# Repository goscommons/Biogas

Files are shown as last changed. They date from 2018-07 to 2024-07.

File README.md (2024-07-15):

# Mesophilic Biodigester
## validated design
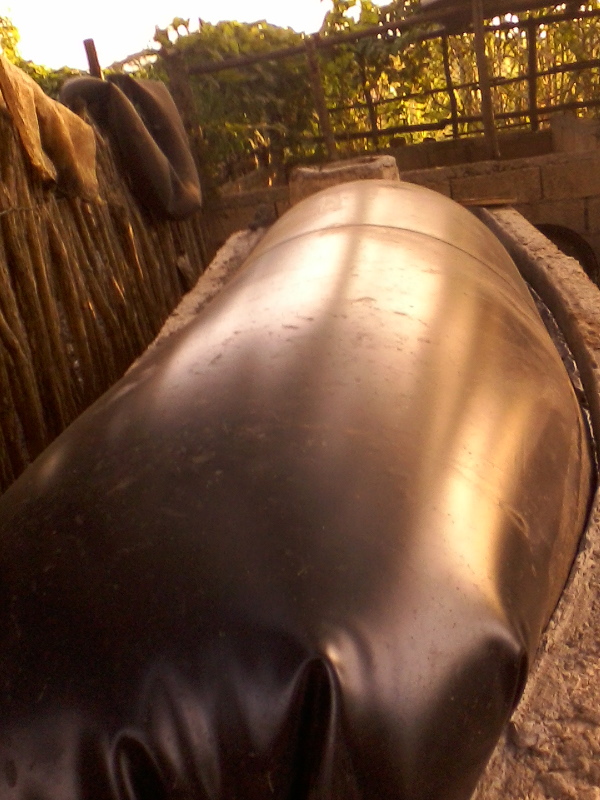
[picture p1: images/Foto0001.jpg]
Name of the machine


For more foto's (and some text) see [Fabrication.md](Fabrication.md).

## Purpose of this digester
Small biodigesters like the one on the foto, made in juli 2018, can be used in the context of family farms to improve life quality in an ecological way. Apart from considerable ecological impact by generating a truly closed loop of resources it also has economical benefits in several ways.
From the various types of installations that exist we chose the Plug-Flow type, the one on the foto cost about 125 dollar in Cuba. Waste generated by humans and/or animals can be processed by this device to produce biogas and fertilizers. This particular type of digester is espcially suitable for tropical and high temperature areas because it works best with a tank liquid temperature of 37 C (99 F).
## How it works
> A biodigester is like a mechanical stomach. It is fed with organic material, which is broken down (decomposed) by micro-organisms (bacteria) in an oxygen-free (anaerobic) environment to produce renewable energy in the form of biogas as well as an exceptionally good fertilizer.
> Anaerobic digestion is a collection of processes by which micro organisms break down biodegradable material in the absence of oxygen.[1] The process is used for industrial or domestic purposes to manage waste and to produce fuel.

## Use context
This biodigester can be used to process pig, cow and other kind of biomatter and probably agricutural waste like banana trees can be digested too.
The biodigester generates economic and ecologic value.
In the first place it produces biogas which can be used for cooking. For this reason these installations are often referred to as biogas plants.
Secondly it produces an excelent natural organic fertilizer that is used for the crops of the farm. This organic fertilizer has the following advantages:
1. It protects and enriches the soil structure in contrast with industrial fertilizers and pesticides.
2. The farmer does not need to buy potasium or other chemical fertilizers.
3. The farmer does not need pesticides anymore or very little because the fertilizer makes the crops healthier and therefore more resistent against deseases and parasites.
4. The crop yield could be higher because the crops are healthier. We will do some testing to see the effect on banana trees.

## Design specifications
- The tank has a size of 300x100x100 cm exterior and 270x70x100 cm interior. The designed liquid hight is about 90 cm giving the installation a total of 1.8 m3 capacity.
- For the outlet any pipe or rigid tube with an inner diameter of 2cm or more can be used.
- The inlet pipe should have an inner diameter of at least 10cm.
- The gas outlet could be placed anywhere on the foil preferably using plastic components and a tube of at least 0.8 cm diameter.
- To attach the foil in a way that no gas can escape we chose to attach it to the tank wall some 40 cm from the top of the wall. Of course when no gas is used the liquid would be pressed down, eventually forcing the gas out of the tank to the air. The gas usage must keep up to the speed at which it is produced.

## References
1. [Retrieved "Remember the biodigester"](https://www.src.sk.ca/blog/remember-biodigester)
1. [Find more in wkikipedia](https://en.wikipedia.org/wiki/Anaerobic_digestion)

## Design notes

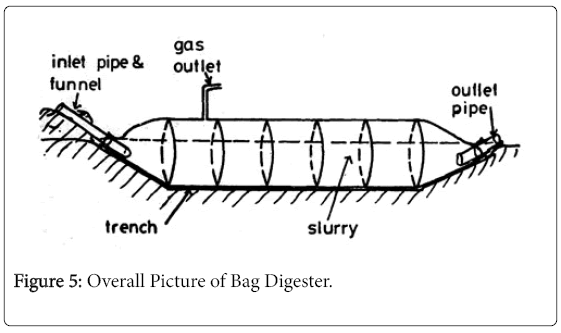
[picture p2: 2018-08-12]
images/functional diagram.png

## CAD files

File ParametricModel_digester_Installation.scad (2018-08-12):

/*A rectangular brick pool that is normally used when bulding small farm biodigesters.*/

// Make an estimate of the size of the digester pool
el=200;//estimated length
ew=100;//estimated width
eh=50;//estimated height

//Adjust brick dimensions
l=21.5;//brick length
w=10.5;//brick width
h=10.5;//brick height

// This section normalizes the dimension between estimate and real brick dimensions
dl=round(el/l)*l;//real length
dw=round(ew/l)*l;// real width
dh=round(eh/h)*h;// real height

// Create wall with proper positioning of bricks
module l_wall(inv,dist,lg,zlg){
    module l_line(dist,lg){
    for (i=[0:lg-1])
      if(i*dist<=dl){
        if(i%2==0){
            translate([0,i*(dist),0])
                cube(size=[w,l,h], center=false);
        }
        else{
            translate([0,i*(dist),0])
            color("red")
            cube(size=[w,l,h], center=false);
        
        }
    }
    else{
        }

}
    if (inv==true)
    for (z=[0:zlg]){
            if(z%2==0){
                translate([0,l/2,z*h])
                l_line(dist,lg);
                }
            else{
                translate([0,0,z*h])
                l_line(dist,lg);
                }
            }    
    else
    for (z=[0:zlg]){
            if(z%2!=0){
                translate([0,l/2,z*h])
                l_line(dist,lg);
                }
            else{
                translate([0,0,z*h])
                l_line(dist,lg);
                } 
        
    }

}


translate([0,0,0])l_wall(false,l,dl/l,dh/h);
translate([dw,0,0])l_wall(true,l,dl/l,dh/h);
translate([0,dl+w,0])rotate([0,0,-90])l_wall(false,l,dw/l,dh/h);
translate([0,w,0])rotate([0,0,-90])l_wall(true,l,dw/l,dh/h);

echo("you need in total: ",round(el/l*2)*round(eh/h)+ round(ew/l*2)*round(eh/h)," bricks to build this pool");

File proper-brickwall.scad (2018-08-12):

/*This is just a very basic model that generates the brick reservoir based on the size of the digester*/

/*Digester Size*/
dl=200;//length
dw=100;//width
dh=50;


/*Brick Parameters*/
h=10.5;//height
w=10.5;//width
l=21.5;//length

i_end=dl/l;
z_end=dw/l;
y_end=dh/h;



//brick line
module l_line(dist){
for (i=[0:i_end])
translate([0,i*(dist+dist*0.05),0])
 cube(size=[w,l,h], center=true);
}

module w_line(dist){
for (i=[0:z_end])
rotate(-90,30,0)
translate([0,i*(dist+dist*0.05),0])
 cube(size=[w,l,h], center=true);
}



// Create wall with proper positioning of bricks
module l_wall(){
    for (i=[0:y_end])
        if (i%2==0){
        translate([0,l/2,i*(h+(h*0.05))])
        l_line(l);
        }
    else{
        translate([0,0,i*(h+(h*0.05))])
        l_line(l);
        }
}

//w_line(l);




l_wall();
//mirror([0,1,0])l_wall();

rotate([0,0,180])
color("lime")
translate([-dw,-dl,0])
l_wall();

//translate([0,0,0])color("red")w_wall();

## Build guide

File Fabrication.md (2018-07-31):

# Biogas
Biogas for small farm

Here are the first photos of the installation. Not much details to be seen here yet, but we are just starting to describe the installation.

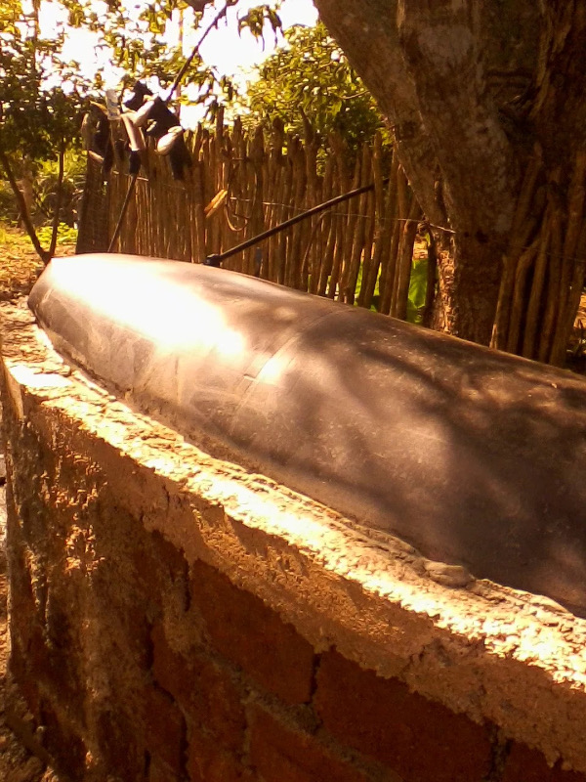
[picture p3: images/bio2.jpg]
Bio gas tank


We used pond foil to cover the tank and hold the gases as produced by the microbes. Since the cover must be air tight, we decided that it would be best to attache it to the tank well below liquid level.

From this photo you can see pieces of electricity (gauge 10) wire coming out of the wall some 40 cm from the top of the tank. These were used to attach the cover. You can also see where the inlet is going to be located.

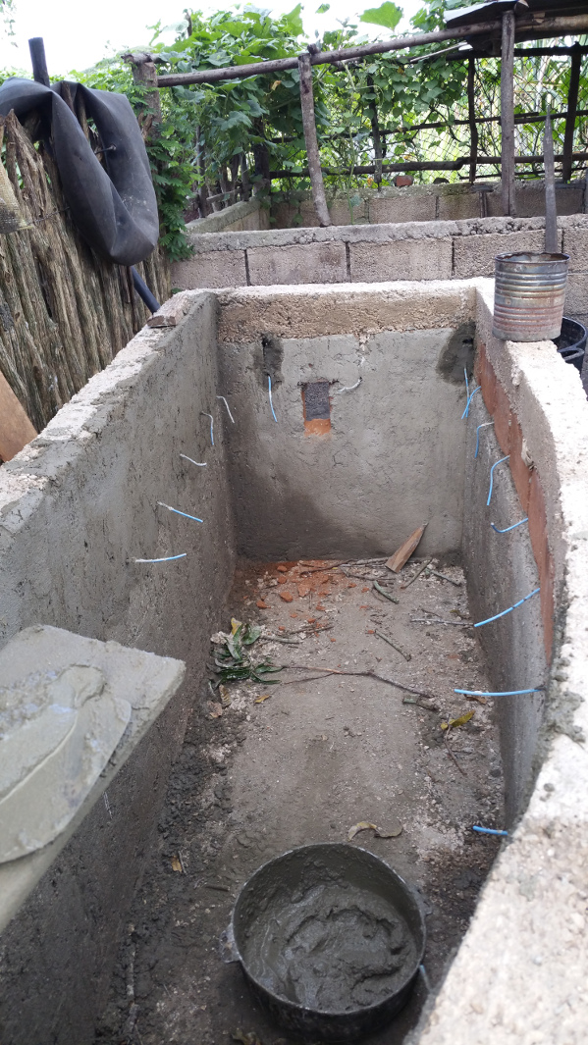
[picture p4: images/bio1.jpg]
Construction of the tank


Here you see a view from the outlet side of the tank. At the far end you can see the inlet mounted on top of the tank border.

Outlet side of the tank

Here you can see the beautiful blue flame of the gas. An installation like this produces about 50 percent methane (MH4) and 50 percent carbon dioxide (CO2), and some, but generally very little hydrogene sulfide (H2S). We have not yet done any filtering. We will add a filter to get rid of the H2S if it turns out to produce a noticeble smell (of rotten eggs).

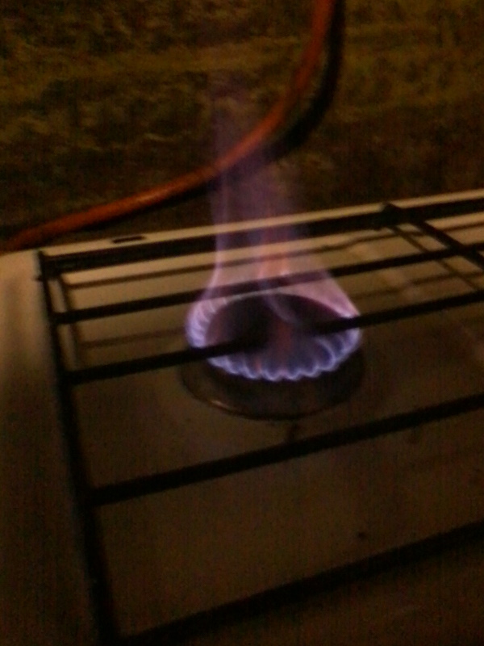
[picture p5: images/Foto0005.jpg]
Flame of the gas stove


Here is another photo of the stove with a pot over the flame.

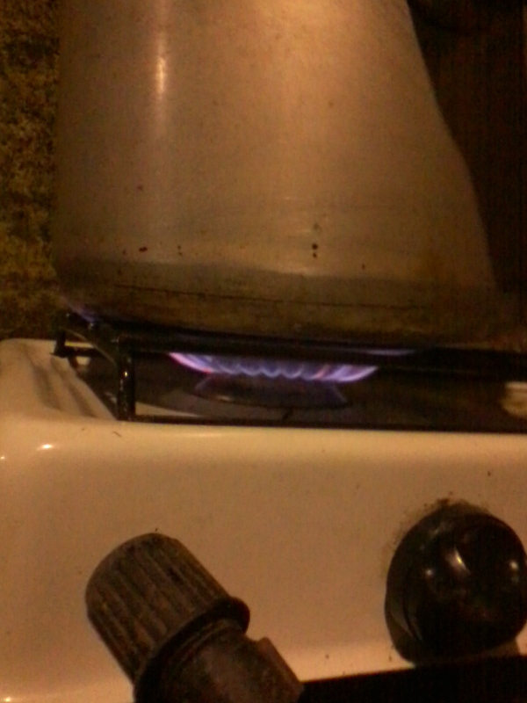
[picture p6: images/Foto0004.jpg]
Flame with pot


Here you can clearly see the inlet. Also you can see here that a rather large part of the liquid is not covered. It would be nice if we could correct this.

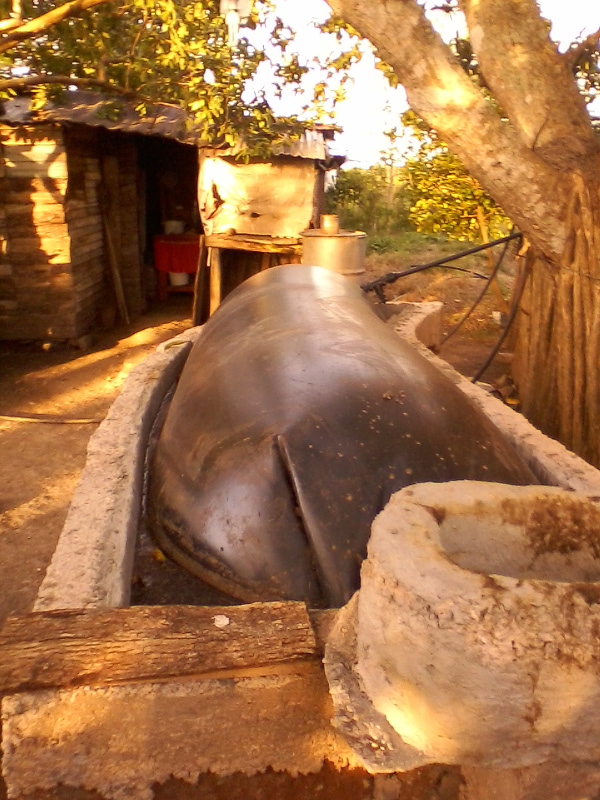
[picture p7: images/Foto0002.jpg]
Inlet side of the tank


And here you see how beautifully curved we made this tank. We thought it could take up less space like this, but it was probably a mistake.

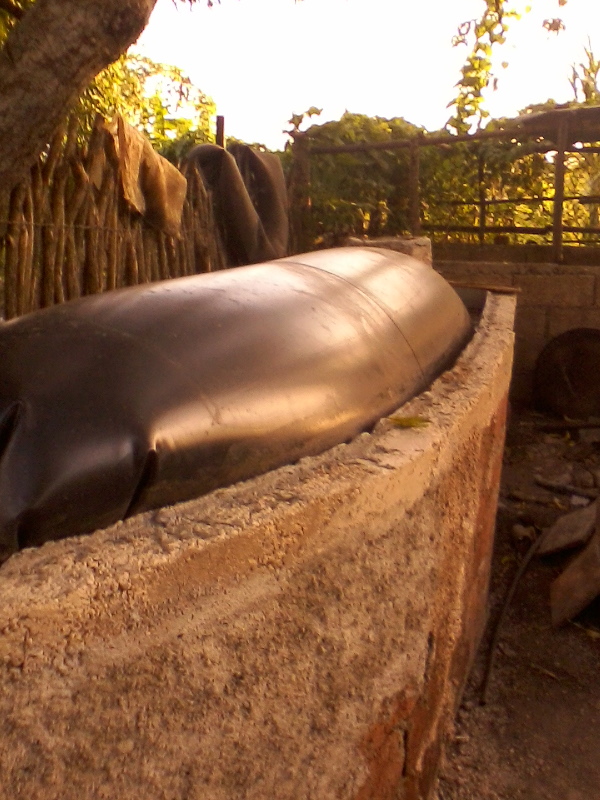
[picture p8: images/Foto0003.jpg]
The tank is curved


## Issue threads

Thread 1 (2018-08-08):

Clear design specification

jurra, 2018-08-08:
Hi Chuck, based on our last meeting, I summarize what we discuss that we can improve in the documentation, I list somethings that need to be done to start completing the documentation. I also open a branch for new documentation.

1. Reuse the template of the CNC machine, or the grapples as a reference to adapt (This I will do)
2. A key thing in the biodigester is how is used, and why is  a good solution for the context you are using it, what are the products that you get from the process, those things you explained.
3. Put proper references and specify as much as possible the context of use of these kinds of digesters, like climate conditions, etc.
4. Start documenting the fabrication process, which is relatively simple to do.
5. I can help in making illustrations that explain the biodigester architecture, how is build.

But the point here is to give a brief introduction, and mainly document how to use the materials her.

I think is also interesting to consider that this design can variate, and adapt. In case people would like to redesign then it would be great to have design recommendations.

Other than that you mentioned that in this context of small farms, gas could be used in tropical contexts to make aircos. This is also an interesting design issue, to outsource through the community.

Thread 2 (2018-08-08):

Design device or method to mix slury

jurra, 2018-08-08:
Maybe @cubar can explain better. But basically we talked about a device that could be introduced in the digester to maintain the slurry mixed inside?

cubar, 2018-08-09:
This is something that we could do ... if and when we feel that it is needed. As for now, it seems that every day the system is producing more gas. Jose Enrique told my brother in law that the pressure of the foil gets "very high" and that the gas is bubbling out from the sides underneath the surface. Well this is normal and secure. I advised him to simply use the gas before it gets lost to the atmosphere. He should begin using it, instead of wood, for cooking for the pigs. Another solution could be a storage bag of one or two m3 but even if he had the foil, there currently is no safe place to store it.

jurra, 2018-08-09:
Very interesting follow up of the digester process. It would be also
usefull to estimate the output of gas per day. :)

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

jurra, 2018-08-09:
If you do a pull you can check the branch I opened. And see the
reorganizarikn of files. As well as a very simple parametric model for the
pool of bricks. You need opensacd to see this.

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

cubar, 2018-08-09:
The info that reach me is a bit confusing for now. A few days ago there was (only) enough gas to cook one hour. But now it seems there is abundance of gas. We have a storage issue. Jose Enrique told me the foil could have been bigger. I think it could have been bigger solving part of the storage problem. But I feel that we should not exaggerate its size to keep the installation hurricane safe.

>> ... It would be also usefull to estimate the output of gas per day. :)
Of course we still need more numbers ;)

jurra, 2018-08-09:
I have also seen solutions where people have an extra storage bag. Smaller
than the one used for the digester, like a buffer

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

cubar, 2018-08-10:
See the last sentence in my first comment ;)

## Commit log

2018-08-08 Added a simple BOM to start estimating costs
    Started doing a sheet to estimate costs, based on possible sizes of the biodigester
    [Biodigester_BOM_Generator.ods]
2018-08-08 Fixed proper amount of bricks
    The formula was wrong
    [Biodigester_BOM_Generator.ods]
2018-08-08 Basic parametric CAD model
    You can use it with freeCAd or openSCAD
    [ParametricModel_digester_Installation.scad]
2018-08-09 Proper Wall patern
    [proper-brickwall.scad]
2018-08-09 Proper responsiveness of length width
    But still not accurate size, because bricks loop is exceeding the size parameters.
    [ParametricModel_digester_Installation.scad]
2018-08-09 Proper positioning of modules, realistic version
    The closure of the 4 walls are sensitive to brick dimensions
    [ParametricModel_digester_Installation.scad]
2018-08-09 Finisihed model for rectangular brick pool
    Now the model gives exact output of construction.
    [ParametricModel_digester_Installation.scad]
2018-08-09 Print the number of bricks needed by the user
    [ParametricModel_digester_Installation.scad]
